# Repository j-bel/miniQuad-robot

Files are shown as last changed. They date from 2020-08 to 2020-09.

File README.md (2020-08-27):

# MiniQuad
### A Mini Quadrupedal Robot
CAD Files, Assembly Instruction, and Software Tutorials for a Miniature Quadrupedal Robot.  

MiniQuad

MiniQuad is a miniature quadruped robot capable of achieving four different leg joint configurations. It was created in order to test the impact of these different configurations on the quadruped's stability when it moves over a flat surface. The robot's body parts have been entirely 3D printed, allowing the robot to be extremely light weight. MiniQuad helps determine the viability of quadruped robots for different robotics research initiatives, as opposed to more traditional, wheeled robots, at a much lower cost.

### Design
The main design goals were to allow multiple leg-joint configurations while minimizing the weight of the robot. In order to do this, we relocated the motors from the joints themselves. The motors on the robot are offset from the joints through the use of timing belts. The motors that control the robot’s knees are actually located at its hip joints, and the motors that control its hip joints are located near the center of the robot’s sides. Apart from using 3D printed components, mounting the actuators on the main body, helped reduce the weight of the legs. Condensing its overall size also helped minimize the robot weight while maximizing the capabilities of the actuators by enabling them to reach higher angular velocities and increasing the overall speed of the robot.

Exploded Leg View

### Assembly

Building a MiniQuad requires access to a 3D printer, a phillips head screw driver, and a pair of pliers.

The Parts List and Links to order all off the shelf parts can be found in the [Master BOM](https://github.com/MiniQuad/robot/blob/master/Master%20BOM.md). 

All of the STL files for 3D printed parts can be found in [STL Files](https://github.com/MiniQuad/robot/tree/master/STL%20Files)

Detailed Assembly Instructions can be found in [Assembly Instructions](https://github.com/MiniQuad/robot/blob/master/Assembly%20Instructions.md)

### Experiments
Details about the experiments conducted can be found in [Experimentation](Experimentation.md)

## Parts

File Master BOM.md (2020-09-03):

<h1>Master BOM</h1>

| Part | Quantity per Robot |  Price | Link
| --- | :---: |--- | --- |
| <h3>Robotis Parts</h3> | | |
| Dynamixel XL-320  | 8 | $175.20 | http://www.robotis.us/dynamixel-xl-320/ |
| OpenCM9.04-C (with onboard XL-type connectors) | 1 | $19.90 | http://www.robotis.us/opencm9-04-c-with-onboard-xl-type-connectors/ |
| Li-ion Battery Charger Set LBB-041 | 2 | $15.80 | http://www.robotis.us/li-ion-battery-charger-set-lbb-041/ |
| Li-ion Battery 3.7V 1300mAh LB-041 | 2 | $19.80 | http://www.robotis.us/li-ion-battery-3-7v-1300mah-lb-041/ |
| <h3>McMaster-Carr Parts</h3> | | |
| 4.4in OD MXL Series Timing Belt  | 4 | $8.37 | https://www.mcmaster.com/7887K13/ |
| 5.6in OD MXL Series Timing Belt  | 4 | $11.60 | https://www.mcmaster.com/7887K15/ |
| Flat Head Screw 4-40 Thread Size, 1-1/4" Long  (50 Pack)| 1 | $4.40 |https://www.mcmaster.com/91771A117 |
| Washer, M2.5 Screw Size, 2.7 mm ID, 6 mm OD (100 pack) | 1 | $1.98 | https://www.mcmaster.com/93475A196/ |
| M2.5 x 0.45mm Thread, 16mm Long (100 pack) | 1 | $4.74 | https://www.mcmaster.com/92000A109/ |
| <h3>Amazon</h3> | | |
| eSUN PLA PRO (PLA+) 3D Printer Filament, Blue | 1 | $23.99 | [Amazon Filament](https://www.amazon.com/eSUN-1-75mm-Printer-Filament-2-2lbs/dp/B01EKEMNRO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) |
| HVAZI #4-40 UNC Machine Screws Nuts Assortment Kit | 1 | $12.99 | [Amazon 4-40 Screw Kit](https://www.amazon.com/HVAZI-Stainless-Phillips-Machine-Assortment/dp/B07GV31SDS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) |
| #4-40 Stainless Hex Lock Nut (100 Pack) | 1 | $6.98 | https://www.amazon.com/gp/product/B07HYNZXGV/ref=ppx_yo_dt_b_search_asin_title?ie=UTF8&psc=1 |
|<h4>Total Cost</h4>| | <h4>$305.75</h4> | |

<br/>
<br/>

<h3>Fasteners</h3>

| Part | Qty. |
| --- | :---: |
| 4-40 x 1.25" Countersunk | 4 |
| 4-40 x .75" Countersunk | 12 |
| 4-40 x .50" Coutnersunk | 16 |
| 4-40 x .375" Coutnersunk | 8 |
| 4-40 Locknut | 24 |
| 4-40 Hex Nut | 16 |
| M2.5 x 16mm | 8 |
| M2.5 Washer | 8 |
<br/>

<h3>3D Printed Parts</h3>

| Part | Filament per (g) | Qty | Filament Total (g)|
| --- | :---: |--- | --- |
| Base | 33.20 | 1 | 33.20 |
| Electronics Mount | 71.33 | 1 | 71.33 |
| Foot | 4 | | |
| Hip Pulley | 5.00 | 4 | 20.00 |
| Hip Pulley Brace | 5.78 | 4 | 23.12 |
| Knee Pulley | .54 | 4 | 2.16 |
| Leg | 1.96 | 4 | 7.84 |
| Leg Cover | 2.25 | 4 | 9.00 |
| Motor Hub | 3.75 | 4 | 15.00 |
| Motor Hub Connector | 3.35 | 4 | 13.40 |
| Thigh | 7.86 | 4 | 31.44 |
| Thigh Cover | 3.48 | 4 | 13.92 |
| XL320 Motor Mounts | 35.94 | 2 | 71.88 |
| Printing Total | | | 312.29 |

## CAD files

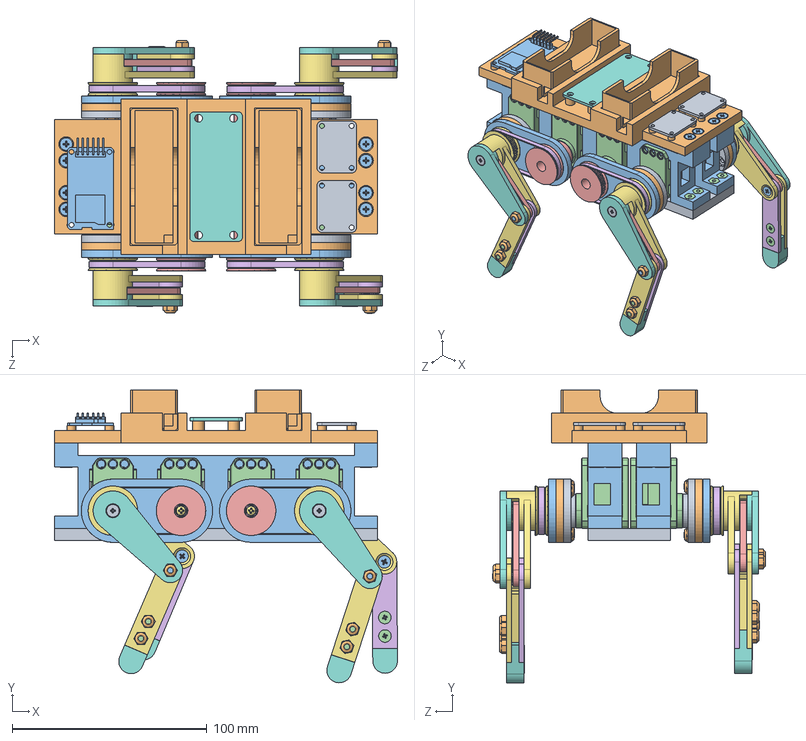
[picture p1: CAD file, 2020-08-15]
CAD/Mini Quad Assembly.SLDASM
176.2 x 150.3 x 140.2 mm
Base
Electronics Mount
XL320 Motor Mount x 2
XL-320 x 8
Hip Pulley x 4
5.6in Timing Belt x 4
Thigh x 4
Thigh Cover x 4
Motor Hub x 4
Motor Hub to Knee Pulley Connector x 4
Hip Pulley Brace x 4
Knee Pulley x 4
4.4in Timing Belt x 4
Leg x 4
Leg Cover x 4
Foot x 4
4-40 x 1.25 x 4
4-40 LockNut x 24
4-40x.75 x 12
4-40x.50 x 16
4-40x.375 x 8
M2.5 Washer x 8
M2.5 x 16mm x 8
Cm904Template
BNO055 9-DOF Orientation Sensor Template x 2
BatteryHolder x 2
sdreader
4-40 Nut x 16

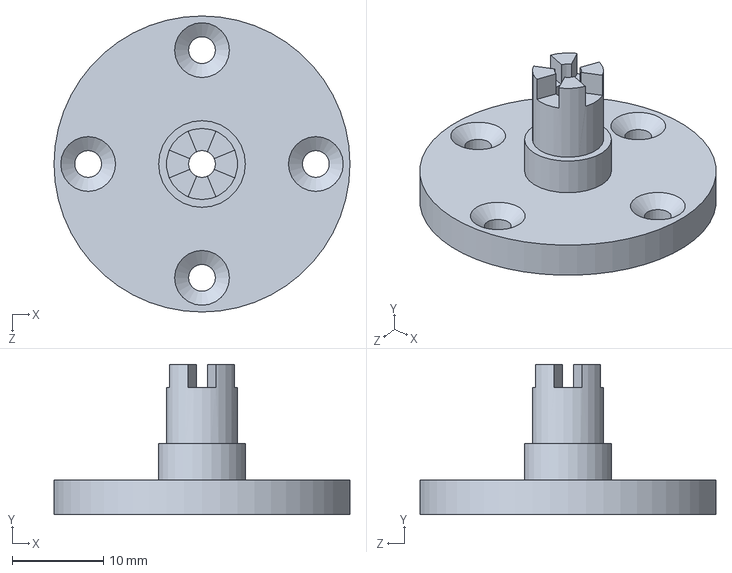
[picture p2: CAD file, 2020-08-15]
CAD/Motor Hub to Knee Pulley Connector.SLDPRT
32.5 x 16.5 x 32.5 mm

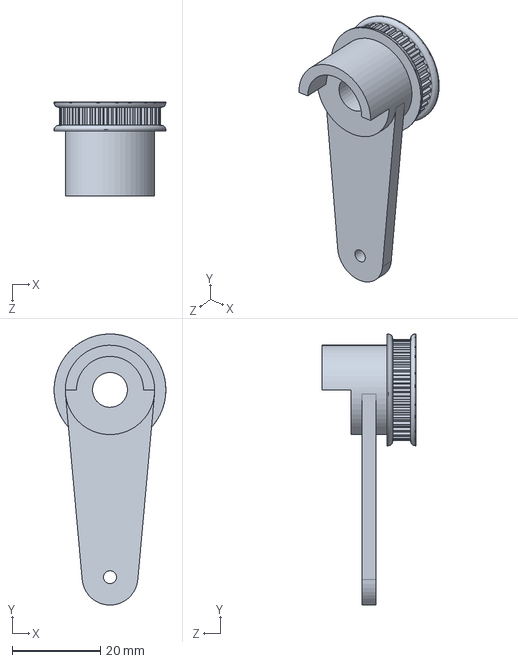
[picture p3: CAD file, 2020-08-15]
CAD/Thigh .SLDPRT
25.4 x 61.6 x 21.5 mm

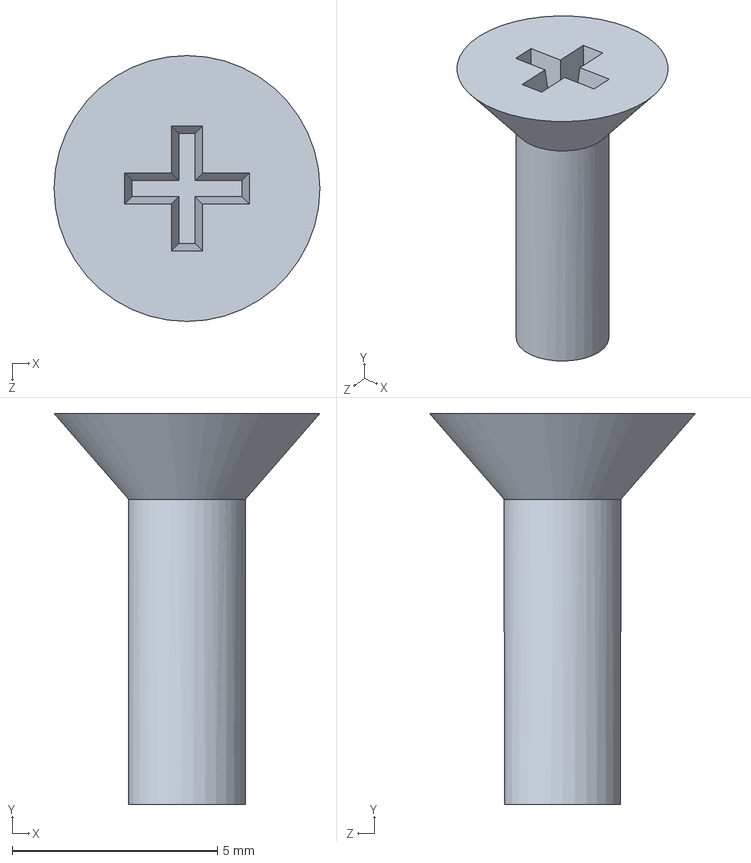
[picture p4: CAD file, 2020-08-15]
CAD/4-40x.375.SLDPRT
6.48 x 9.52 x 6.48 mm

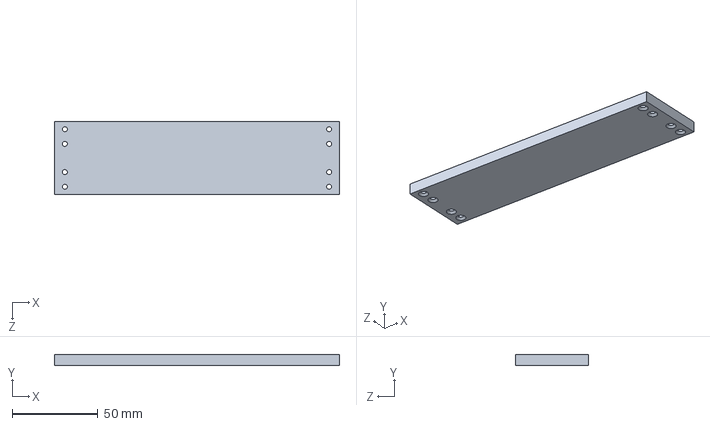
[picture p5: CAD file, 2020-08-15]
CAD/Base.SLDPRT
166.0 x 6.35 x 42.5 mm

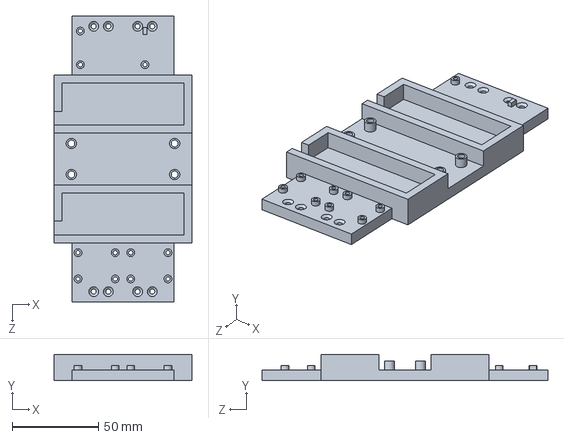
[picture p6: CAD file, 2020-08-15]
CAD/Electronics Mount.SLDPRT
80.0 x 15.4 x 166.0 mm

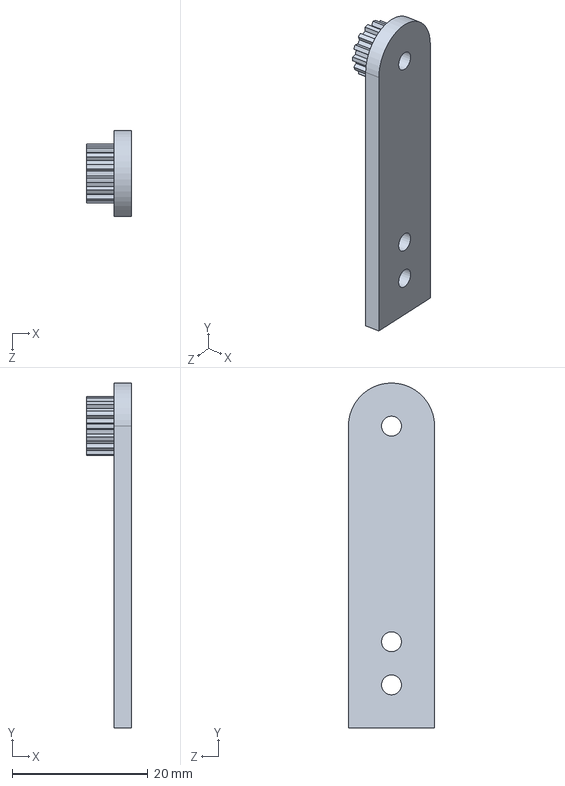
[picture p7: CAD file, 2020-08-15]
CAD/Leg.SLDPRT
6.60 x 50.8 x 12.7 mm

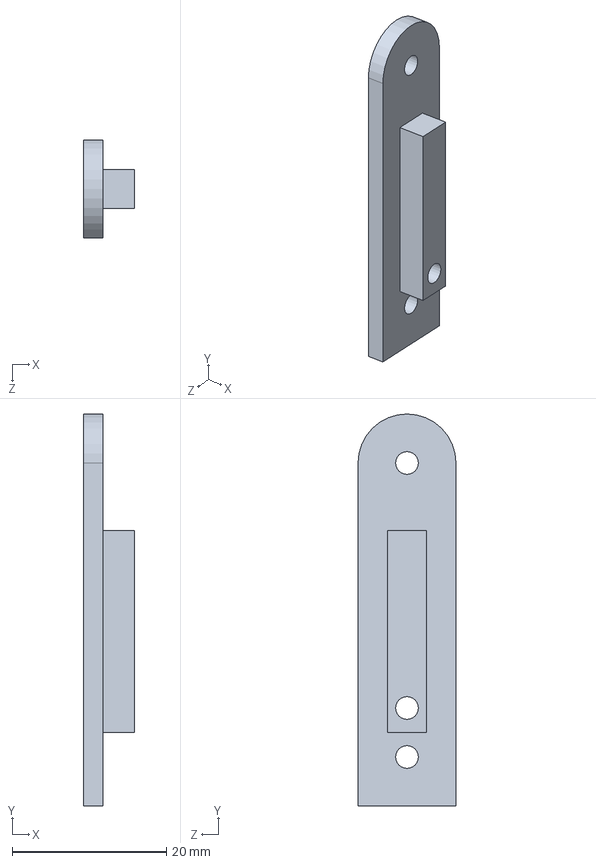
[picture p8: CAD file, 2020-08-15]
CAD/Leg Cover.SLDPRT
6.60 x 50.8 x 12.7 mm

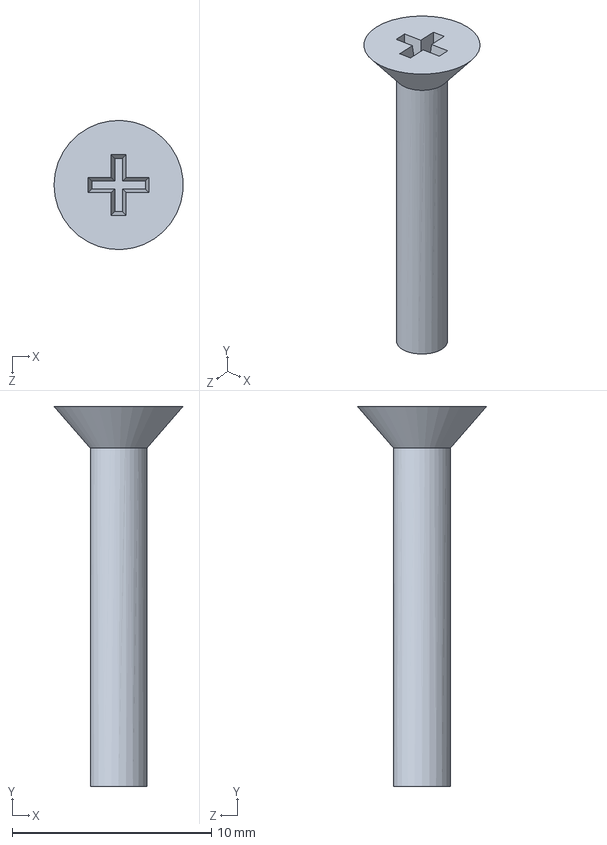
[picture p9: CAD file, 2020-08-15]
CAD/4-40x.75.SLDPRT
6.46 x 19.1 x 6.47 mm

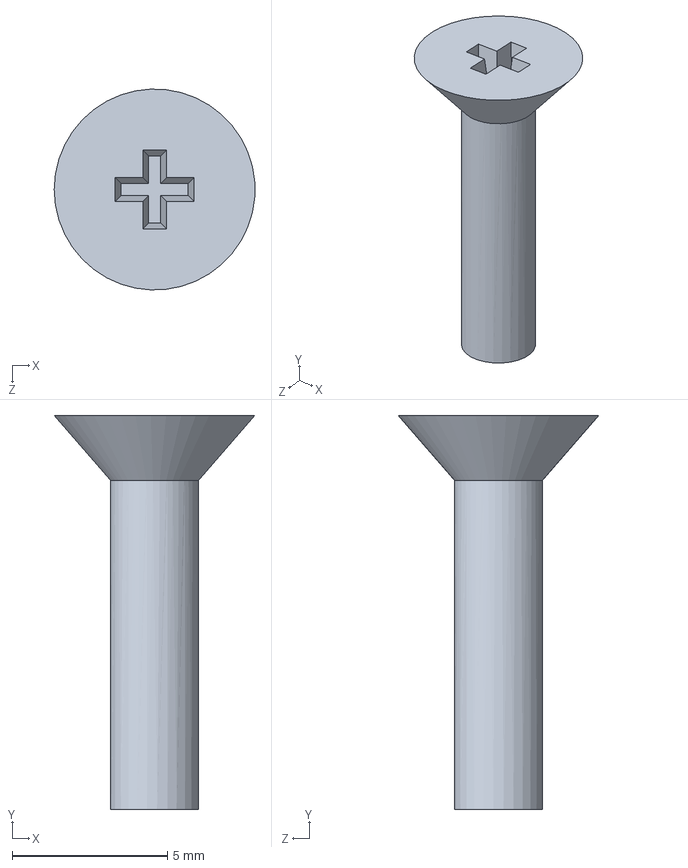
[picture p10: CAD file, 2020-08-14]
CAD/4-40x.50.SLDPRT
6.47 x 12.7 x 6.47 mm

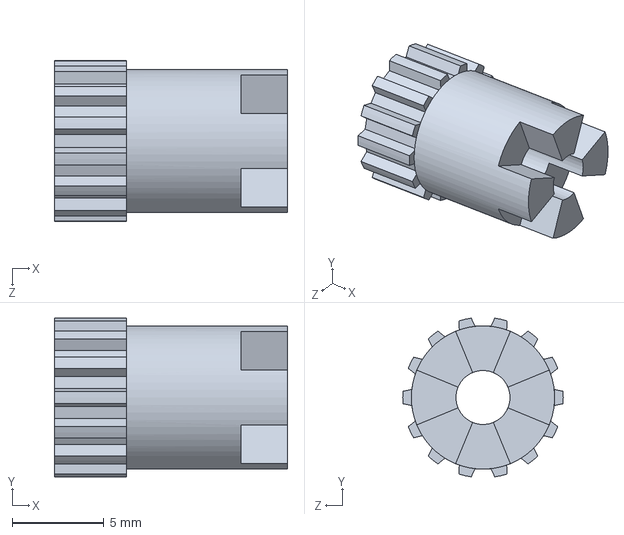
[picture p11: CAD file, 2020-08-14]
CAD/Knee Pulley.SLDPRT
12.7 x 8.66 x 8.75 mm

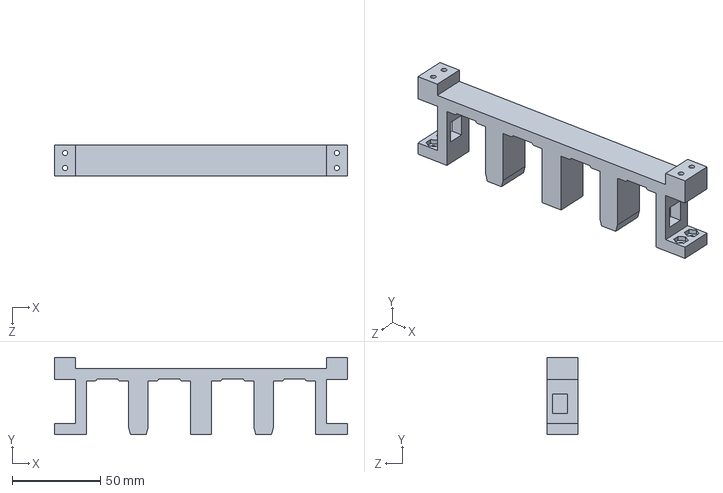
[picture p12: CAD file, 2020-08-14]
CAD/XL320 Motor Mount.SLDPRT
166.0 x 43.9 x 17.5 mm

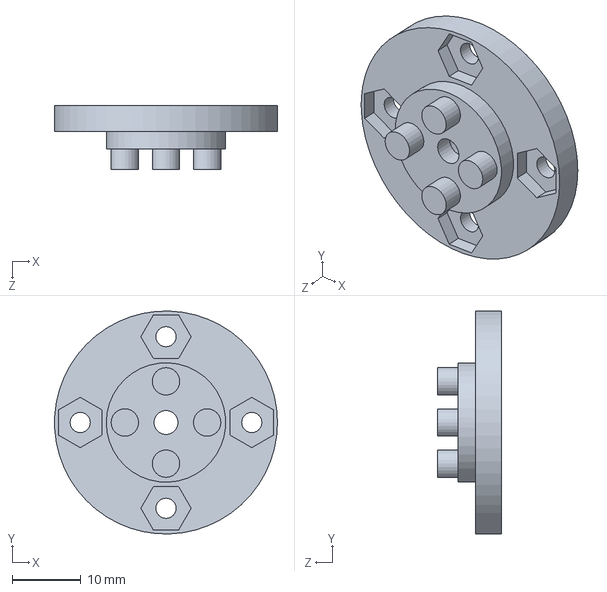
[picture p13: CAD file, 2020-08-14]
CAD/Motor Hub.SLDPRT
32.5 x 32.5 x 9.35 mm

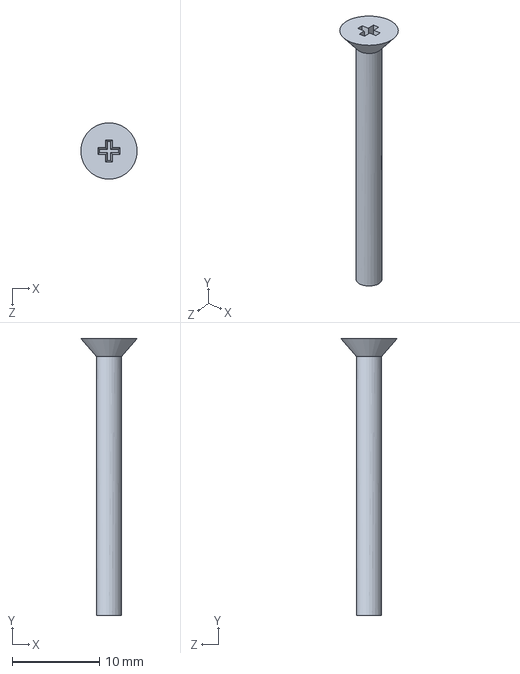
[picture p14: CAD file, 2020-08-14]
CAD/4-40 x 1.25.SLDPRT
6.48 x 31.8 x 6.48 mm

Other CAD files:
CAD/Foot.SLDPRT
CAD/5.6in Timing Belt.SLDPRT
CAD/Cm904Template.SLDPRT
CAD/BatteryHolder.SLDPRT
CAD/4-40 LockNut.SLDPRT
CAD/4-40 Nut.SLDPRT
CAD/4.4in Timing Belt.SLDPRT
CAD/BNO055 9-DOF Orientation Sensor Template.SLDPRT
CAD/Hip Pulley Brace.SLDPRT
CAD/Hip Pulley.SLDPRT
CAD/M2.5 Washer.SLDPRT
CAD/M2.5 x 16mm.SLDPRT
CAD/Thigh Cover.SLDPRT
CAD/XL-320.SLDPRT
CAD/sdreader.SLDPRT
STL Files/Base.STL
STL Files/Electronics Mount.STL
STL Files/Hip Pulley Brace.STL
STL Files/Hip Pulley.STL
STL Files/Knee Pulley.STL
STL Files/Leg Cover.STL
STL Files/Leg.STL
STL Files/Motor Hub to Knee Pulley Connector.STL
STL Files/Motor Hub.STL
STL Files/Thigh .STL
STL Files/Thigh Cover.STL
STL Files/XL320 Motor Mount.STL

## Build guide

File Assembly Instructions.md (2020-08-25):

# Assembly Instructions

#### Print and Acquire Parts

Begin by gathering all of the necessary material to build MiniQuad found in the [Master BOM](https://github.com/MiniQuad/robot/blob/master/Master%20BOM.md). Print the supplied [STL Files](https://github.com/MiniQuad/robot/tree/master/STL%20Files) in the quantities listed in the [Master BOM](https://github.com/MiniQuad/robot/blob/master/Master%20BOM.md). Note that all parts were sliced in the [PrusaSlicer](https://www.prusa3d.com/prusaslicer/) and printed on a [Prusa MK3S](https://shop.prusa3d.com/en/3d-printers/180-original-prusa-i3-mk3s-kit.html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) with a 40% infill. Depending on your slicer settings and 3D Printer, material used for each part can vary. You also may need to edit the parts depending on the tolerances of your 3D printer. SOLIDWORKS files are included in the [CAD](https://github.com/MiniQuad/robot/tree/master/CAD) folder in case edits are necessary.

#### Download OpenCM IDE

While the parts are printing, follow the steps to download the [OpenCM IDE](https://emanual.robotis.com/docs/en/software/opencm_ide/getting_started/) from robotis. The OpenCM IDE will be necessary to run the initial set up code as well as program MiniQuad to move. 

#### Assign Motor ID's
Follow the Steps in the [Assign Motor ID Instructions](https://github.com/MiniQuad/robot/blob/master/Assembly%20Files/1%20Assign%20Motor%20ID's.md) to assign each of the 8 motor's with an individual ID that will be later used to program MiniQuad.

#### Main Body Assembly
Follow the Steps in the [Main Body Assembly Instructions](https://github.com/MiniQuad/robot/blob/master/Assembly%20Files/2%20Main%20Body%20Assembly.md) to assemble the body of MiniQuad and attach all of the motors in the correct locations.

#### Leg Assembly
Follow the Steps in the [Leg Assembly Instructions](https://github.com/MiniQuad/robot/blob/master/Assembly%20Files/3%20Leg%20Assembly.md) to attach and assemble all of the legs on MiniQuad.

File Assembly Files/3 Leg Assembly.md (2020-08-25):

### Leg Assembly

Plug two batteries into the OpenCM9.04. Open the [SetZeroPosition](https://github.com/MiniQuad/robot/blob/master/Assembly%20Files/Assembly%20Code/SetZeroPosition.ino) code in the OpenCM IDE. Replace the numbers in the red box below to the numbers of the motors that you are currently assembling a leg on. The leg assembly shown in the instructions below correspond to motors 1 and 2. Upload the code to the OpenCM9.04. 

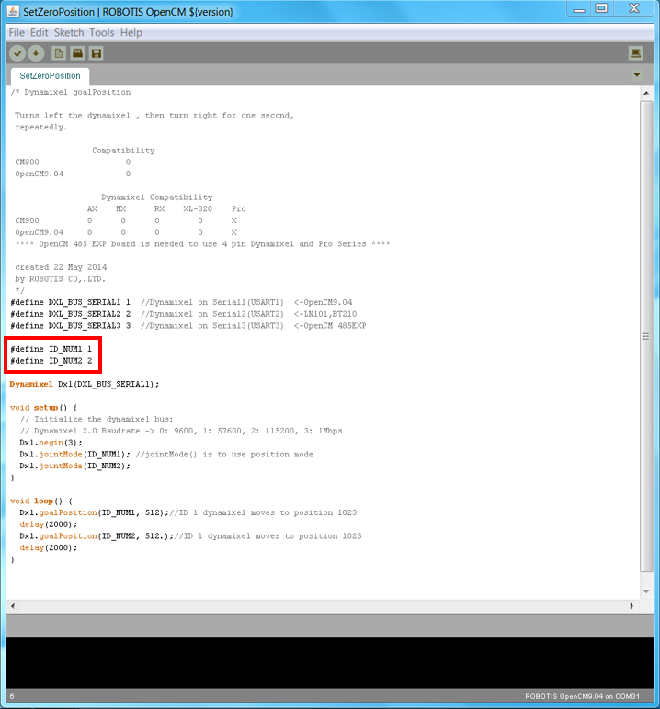
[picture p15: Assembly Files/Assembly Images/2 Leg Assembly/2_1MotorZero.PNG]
2_1MotorZero


Once the Code is uploaded, the motor should move to the position shown below where the notch on the base of the motor aligns with the notch on the horn of the motor. You can assemble the legs with the batteries and OpenCM9.04 unplugged, but it is recommended to leave them plugged in to prevent the motors from rotating at all during the assembly.

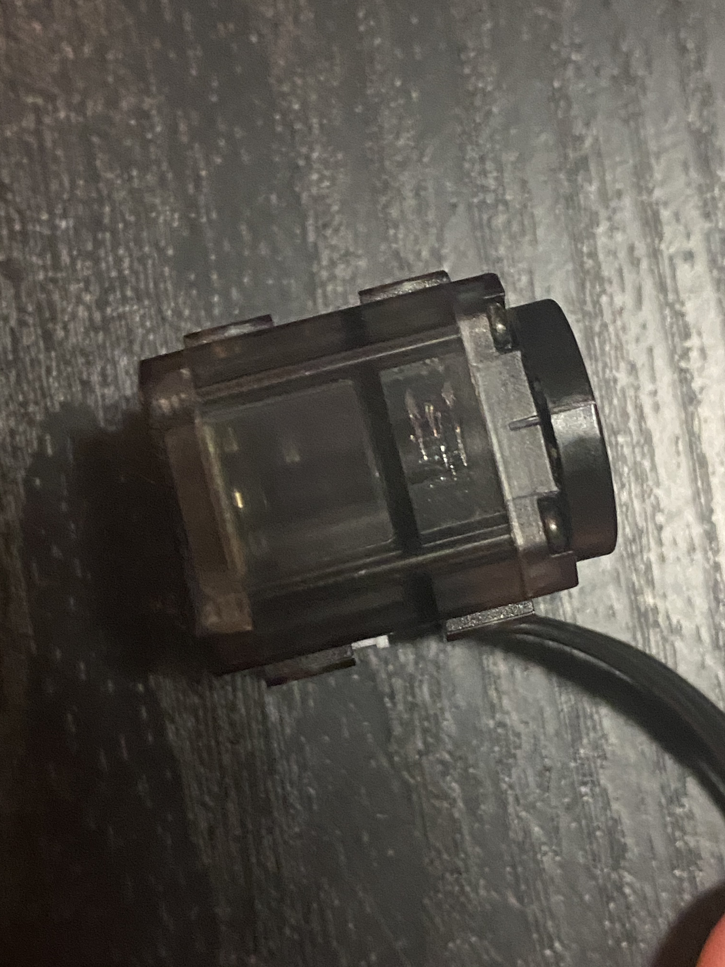
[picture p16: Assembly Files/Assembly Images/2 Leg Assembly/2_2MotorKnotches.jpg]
2_2MotorKnotches


Remove the screws from the XL-320 that hold the servo horn in place (circled below)

1RemoveScrew

Place 4-40 nuts (x2) into 2 of slots on the back of the Motor Hub. Any set of slots will work as long as they are both on the same diagonal of the rectangle formed by the 4 slots present.

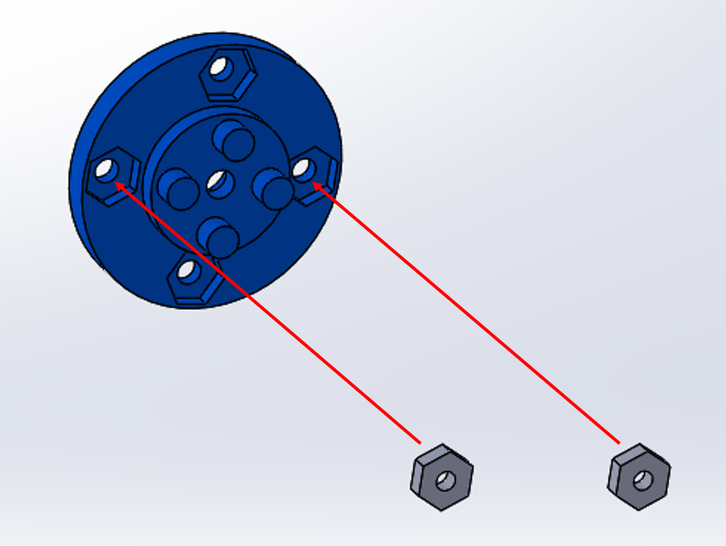
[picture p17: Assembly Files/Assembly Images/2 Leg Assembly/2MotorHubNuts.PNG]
2MotorHubNuts


Attach the Motor Hub to the horn of the XL-320. First press the Motor Hub into place. The registration tabs on the Motor Hub should align with the holes on the horn of the XL-320. Snap the tabs into place and fasten the hub onto the motor using an M2.5 x 16mm screw and an M2.5 Washer.

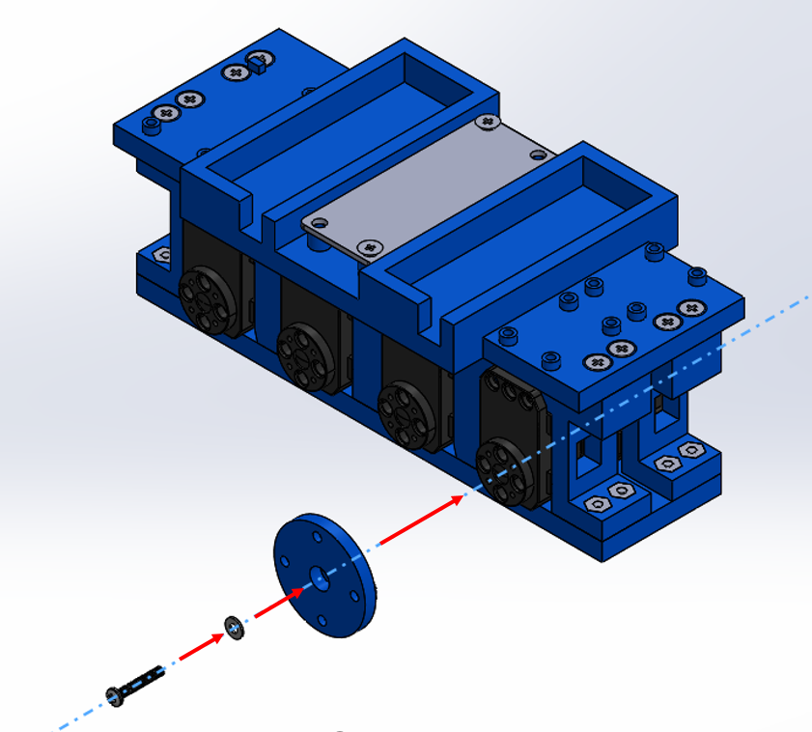
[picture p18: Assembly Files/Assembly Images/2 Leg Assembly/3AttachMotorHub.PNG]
3AttachMotorHub


Place a 4-40 Locknut into the slot on the back of the Motor Hub Connector. Make sure to push the Locknut as far into the connector as possible.

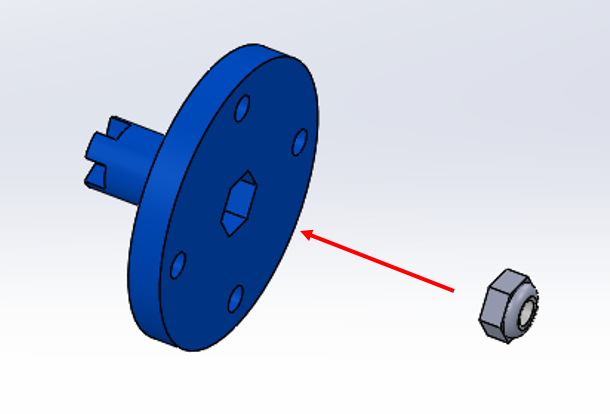
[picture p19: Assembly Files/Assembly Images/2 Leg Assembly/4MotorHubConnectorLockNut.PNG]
4MotorHubConnectorLockNut


Attach the Motor Hub Connector to the Motor Hub using 4-40 x .375" countersunk screws (x2). 

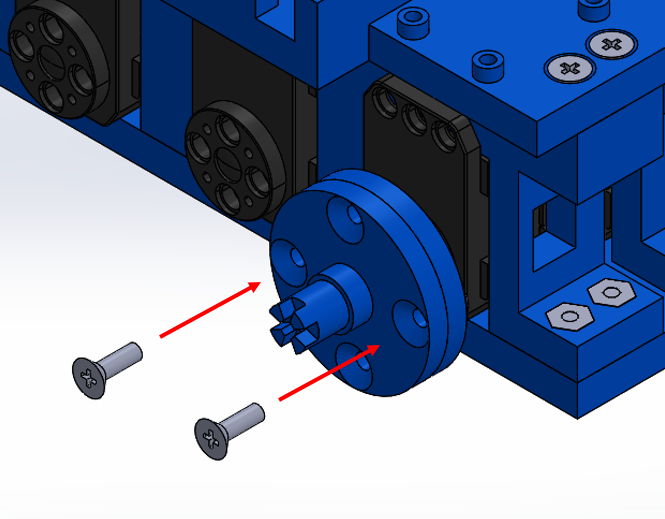
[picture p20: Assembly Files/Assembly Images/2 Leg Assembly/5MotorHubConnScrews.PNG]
5MotorHubConnScrews


Attach the Pulley Brace to the assembly by sliding the smaller hole of the brace onto the Motor Hub Connector.

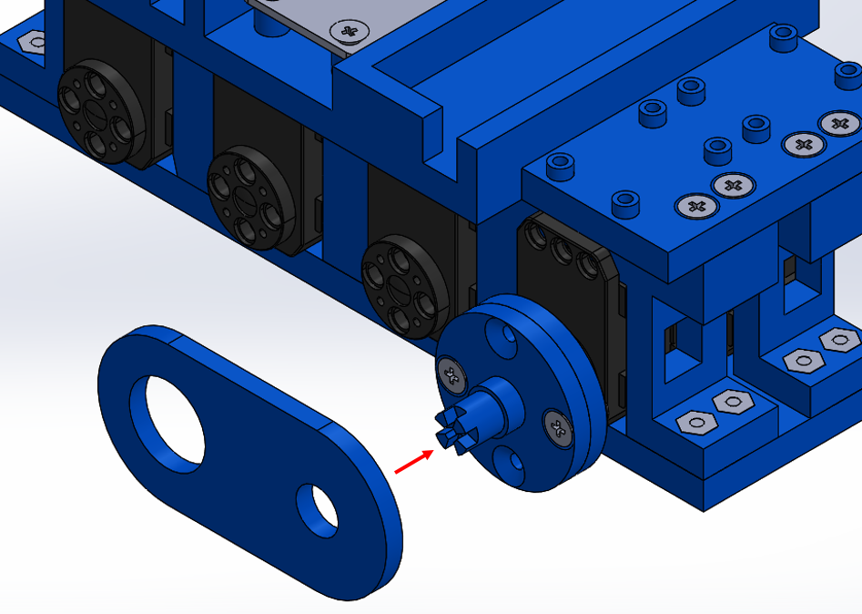
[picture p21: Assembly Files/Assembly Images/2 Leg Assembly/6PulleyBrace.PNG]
6PulleyBrace


Attach the Thigh Pulley to the assembly following the same steps as the Motor Hub. Align the registration tabs on the Thigh Pulley with the holes on motor 2 and snap it into place. Fasten the pulley to the motor using an M2.5 x 16mm screw and an M2.5 Washer.

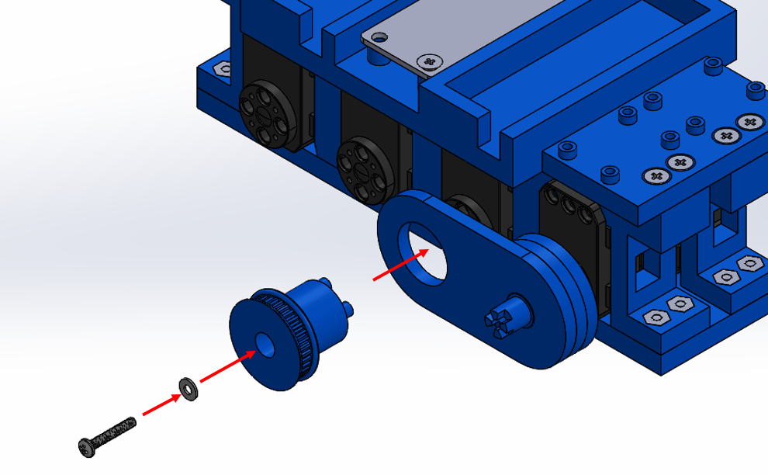
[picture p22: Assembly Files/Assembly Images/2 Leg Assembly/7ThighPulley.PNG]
7ThighPulley


Attach the 5.6" Timing Belt and Thigh to the Assembly. Wrap one end of the timing belt around the Thigh. Hold the thigh vertical to the assembly. Wrap the belt around the Thigh Pulley while sliding the thigh onto the Motor Hub Connector. Keep the thigh as vertical as possible during installation. Some deviation will be necessary to engage the timing belt. This will be corrected later during Motor Calibration.

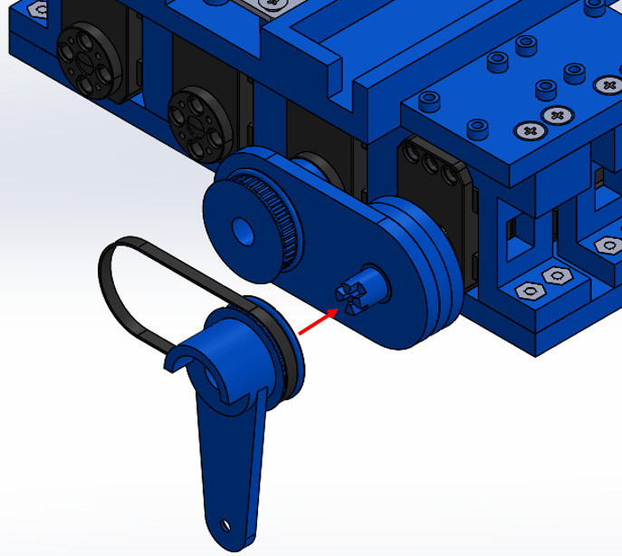
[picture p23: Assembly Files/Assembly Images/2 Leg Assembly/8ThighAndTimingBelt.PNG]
8ThighAndTimingBelt


Attach the Knee Pulley to the assembly by sliding it into the hole on the front of the Thigh. Align the registration tabs on the Knee Pulley to the slots on the Motor Hub Connector. Snap the Knee Pulley into place. The images on the right below depict the assembly with the Knee Pulley fully inserted into the leg assembly. The face of the teeth on the Knee Pulley should be sitting up agains the face of the thigh as seen in the bottom right image. 

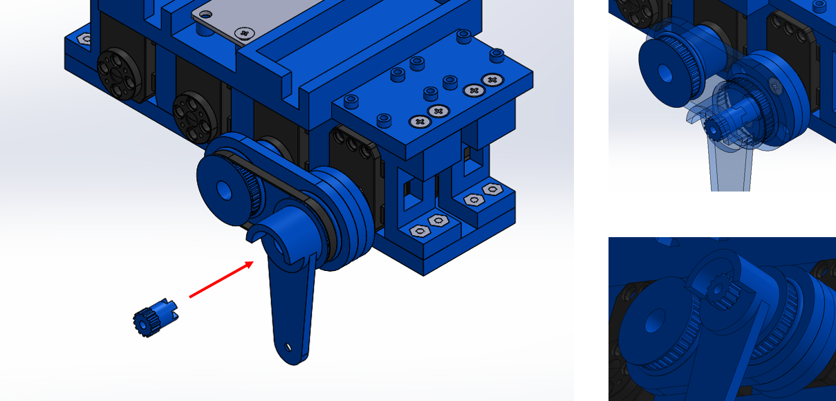
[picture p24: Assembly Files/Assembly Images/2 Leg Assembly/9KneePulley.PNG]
9KneePulley


Attach the Knee Cover to the Knee using a 4-40 x .5" countersunk screw and a 4-40 Locknut. Fasten the leg cover into place, but leave it loose enough for the Knee Cover to rotate around the axis of the screw.

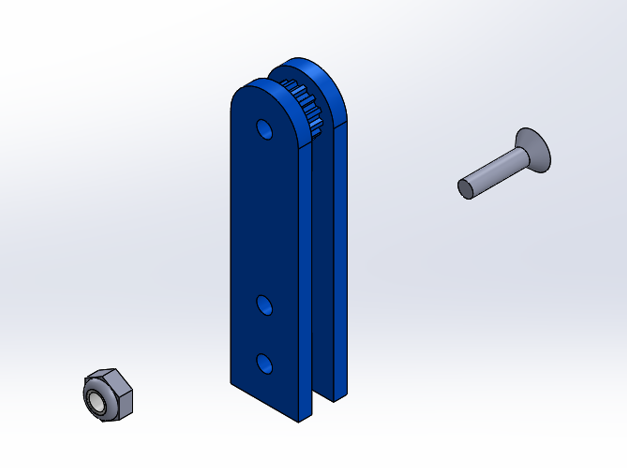
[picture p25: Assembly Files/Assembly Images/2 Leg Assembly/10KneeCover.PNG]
10KneeCover


Rotate the Knee Cover to one side enough to allow the 4.4" Timing Belt onto the teeth of the Knee.

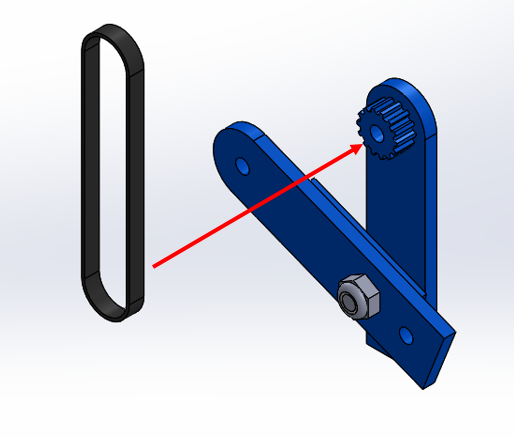
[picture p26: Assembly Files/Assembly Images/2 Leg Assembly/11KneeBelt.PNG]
11KneeBelt


Rotate the Knee Cover Back into place. Place the timing belt around the Knee Pulley at the top of the leg assembly. Stretch the Knee and Knee Cover downwards and put a 4-40 x .75" countersunk screw into the back of the Knee. If the fit is too tight, you may need to twist the screw into place. Make sure the back face of the knee is pressing up against the face of the Thigh.

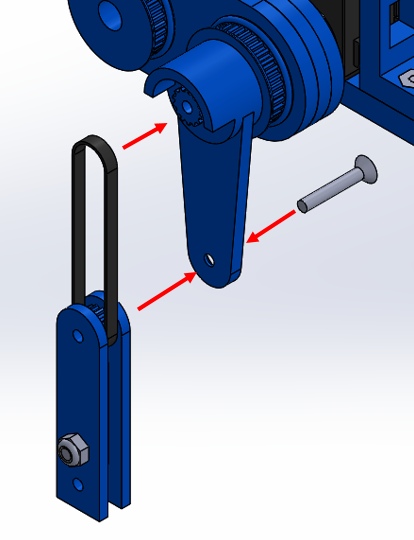
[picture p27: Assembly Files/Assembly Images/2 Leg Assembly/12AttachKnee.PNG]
12AttachKnee


Place the Thigh Cover onto the end of the 4-40 x .75" screw used in the previous step. Tighten it into place with a 4-40 Locknut. Make sure that the screw is not to tight and that the Thigh Cover can be rotated about the screw.

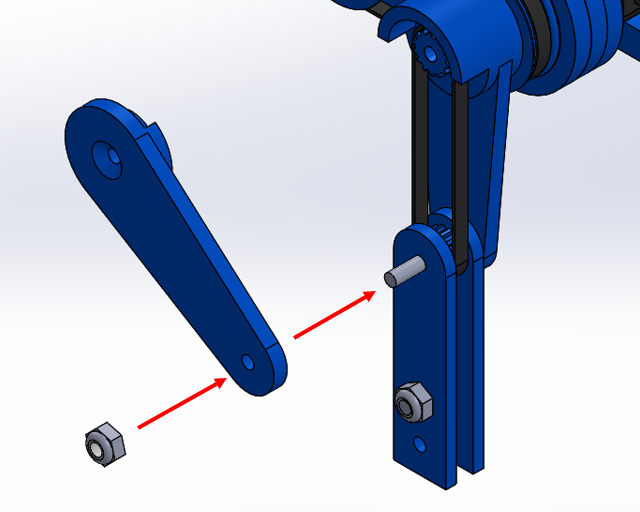
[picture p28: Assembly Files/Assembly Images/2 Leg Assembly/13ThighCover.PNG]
13ThighCover


Push on the bottom of the Knee in the direction and location of the yellow arrow in the image below. Rotated the top of the Thigh Cover into place. If the faces on the Thigh Cover don't sit flush against the faces of the Thigh, you made need to push more on the bottom of the foot. The assembly with flex a little bit, but do not push too hard as you may risk damaging the parts. Once the Thigh Cover is in place, fasten the assembly together using a 4-40 x 1.25" countersunk screw.

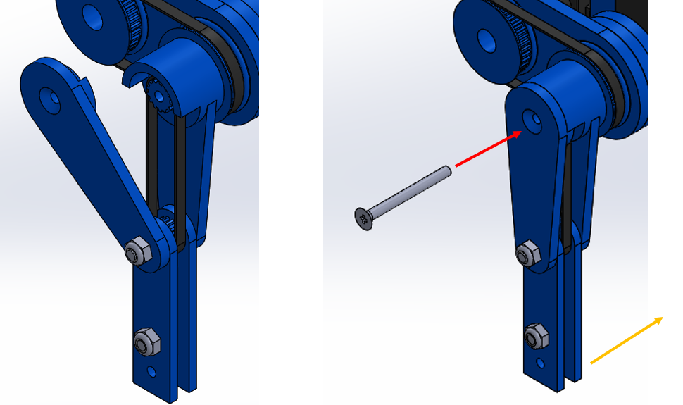
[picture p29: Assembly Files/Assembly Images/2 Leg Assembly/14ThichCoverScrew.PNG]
14ThichCoverScrew


Attach the foot to the assembly. Slide the Foot into place and tighten it to the bottom holes od the Knee and Knee Cover using a 4-40 x .50" countersunk screw and a 4-40 Locknut.

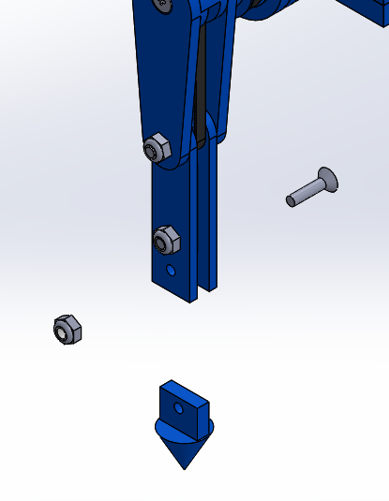
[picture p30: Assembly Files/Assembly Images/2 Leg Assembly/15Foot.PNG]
15Foot


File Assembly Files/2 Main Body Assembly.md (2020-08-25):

### Main Body Assembly

Lay the motors out in the orientation in the image below. 

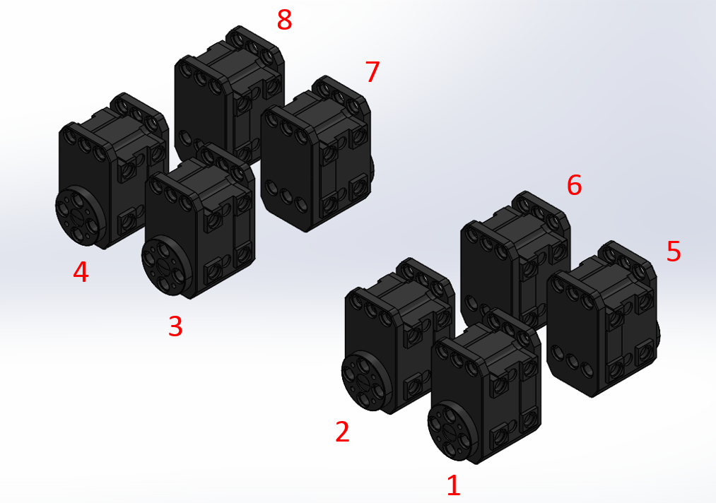
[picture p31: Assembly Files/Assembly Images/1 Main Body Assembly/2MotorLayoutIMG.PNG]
2MotorLayoutIMG


Connect Motor 1 to 2, 3 to 4, 5 to 6, and 7 to 8 with one of the supplied cables using inner terminals between each respective set of motors. Connect a second cable to the other terminals of motors 2, 3, 6, and 7. These terminals will be closest to the center of motor layout pictured above. Leave one end of the cable unnattached. This will be used to connect to the controller later.

Press a 4-40 Nut into each of the 4 holes on one of the XL320 Motor Mounts. 

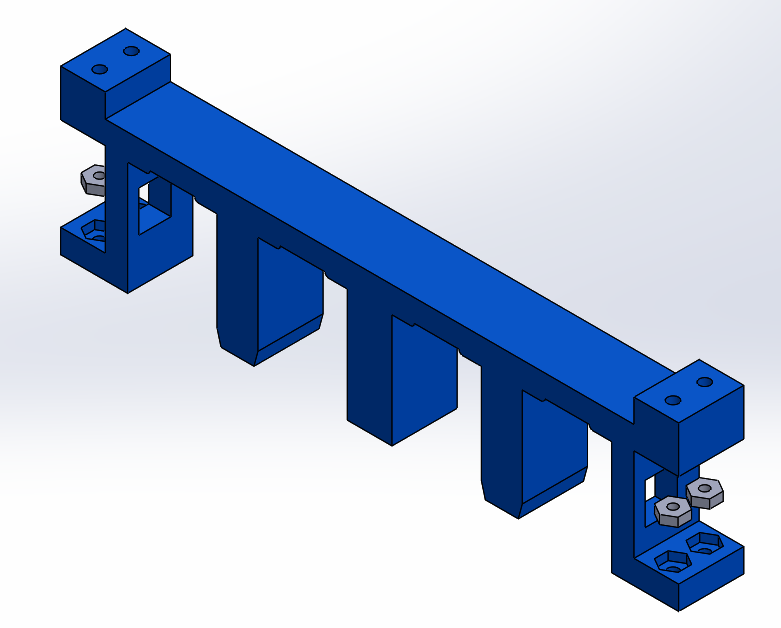
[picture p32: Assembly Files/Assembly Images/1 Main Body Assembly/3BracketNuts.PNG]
3BracketNuts


Slide Motors 1-4 into the bracket as shown below.

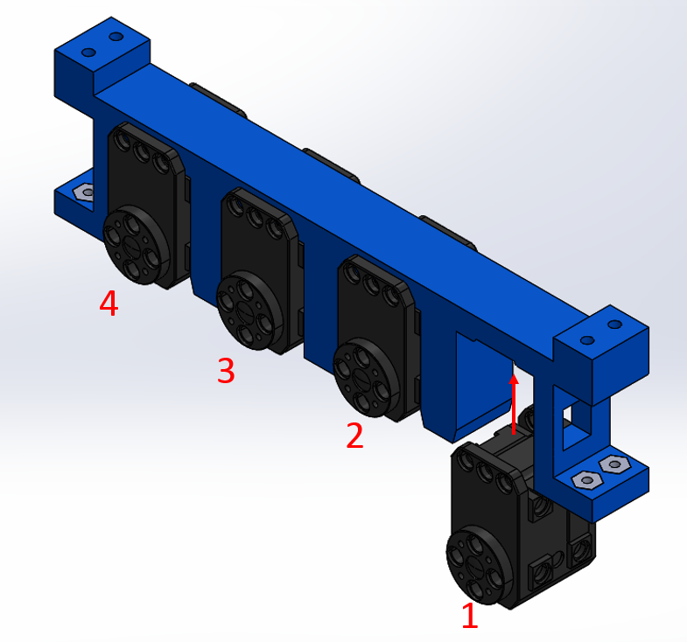
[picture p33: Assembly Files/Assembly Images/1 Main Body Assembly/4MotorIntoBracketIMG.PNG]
4MotorIntoBracketIMG


Repeat the previous 2 steps with motors 5-8. Note the Orientation and order of the motors when assembling.

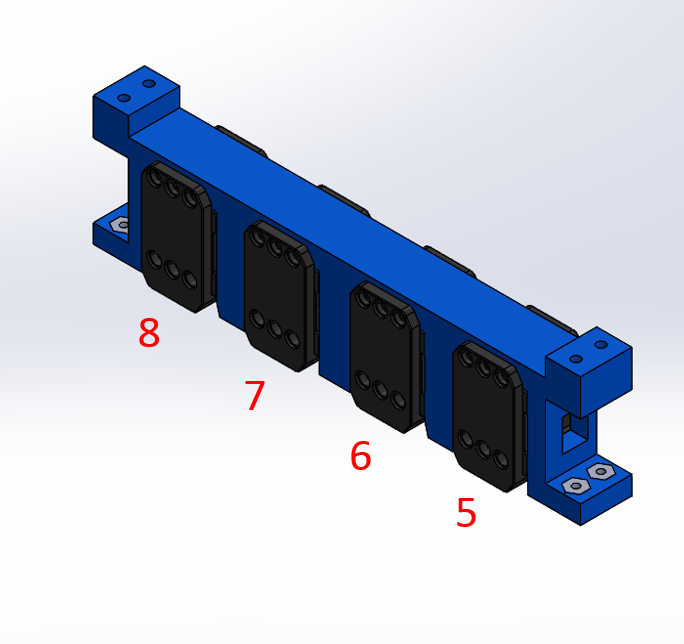
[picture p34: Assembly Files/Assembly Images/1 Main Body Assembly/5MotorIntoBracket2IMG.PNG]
5MotorIntoBracket2IMG


Attach both of the motor brackets to the base plate using 4-40 x .50" screws with countersunk heads (x8).

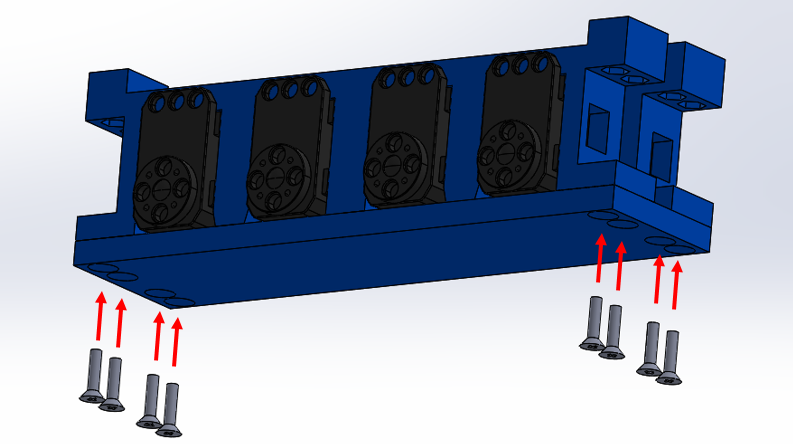
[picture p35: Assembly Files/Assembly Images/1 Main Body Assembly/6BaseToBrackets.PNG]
6BaseToBrackets


Attach the OpenCM9.04 board to the Electronics Mount using 4-40 x .50" screws. These can be countersunk, but flatheads are preferred. Note: other screw lengths over .50" may work as well.

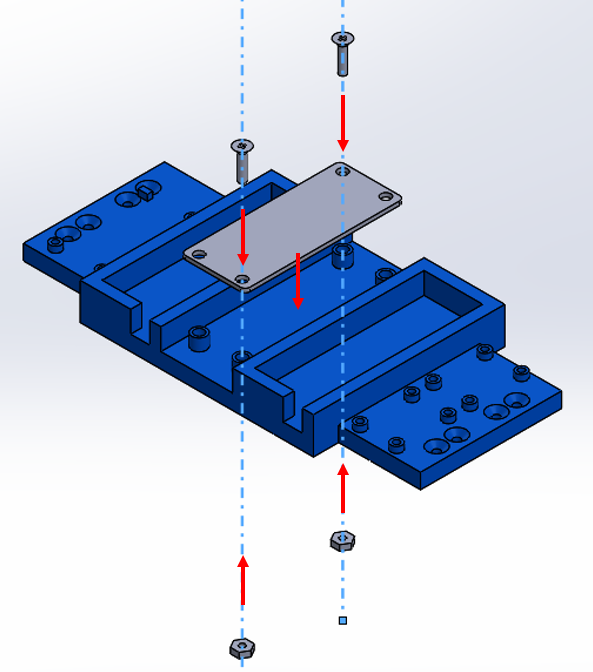
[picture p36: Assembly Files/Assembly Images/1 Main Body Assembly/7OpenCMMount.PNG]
7OpenCMMount


Attach the electronics mount to the assembly using 4-40 x .75" countersunk screws (x8) and 4-40 nuts (x8).

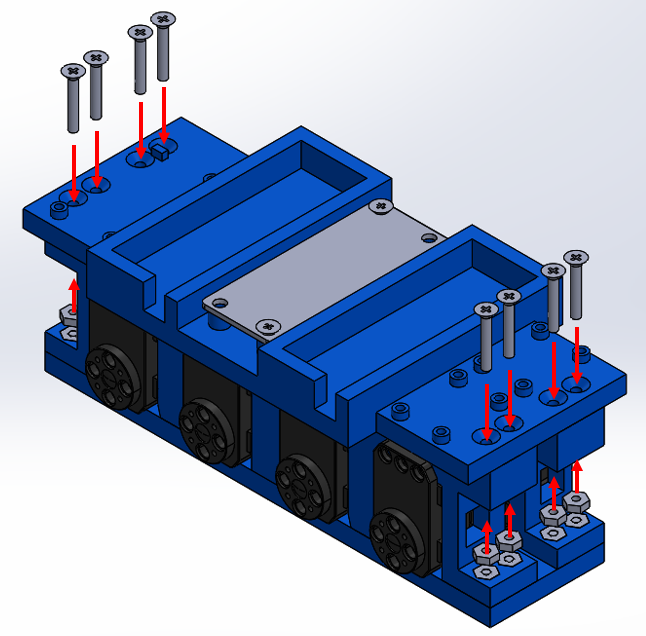
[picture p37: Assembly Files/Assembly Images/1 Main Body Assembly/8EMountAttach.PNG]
8EMountDOwn


After completing the above steps, the assembly should look as follows with the motor ID's corresponding to the numbers in the image below.

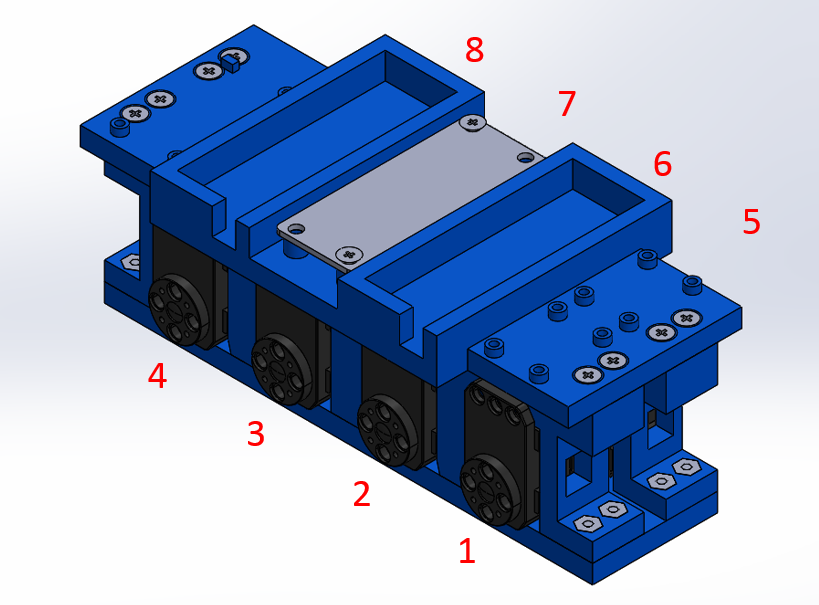
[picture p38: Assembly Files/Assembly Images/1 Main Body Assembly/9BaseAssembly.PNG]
9BaseAssembly


To finish the Main Body Assembly, plug the 4 remaining unconnected 3-wire cables into the 4 ports on the OpenCM 9.04 highlighted below
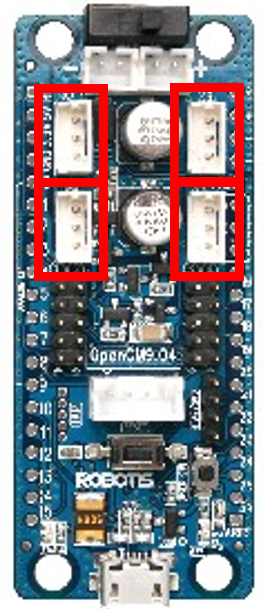
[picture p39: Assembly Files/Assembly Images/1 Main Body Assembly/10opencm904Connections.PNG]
10opencm904Connections


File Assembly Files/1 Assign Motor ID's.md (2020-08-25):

### Assign Motor ID's

Download and open [XL320_SetID](https://github.com/MiniQuad/robot/blob/master/Assembly%20Files/Assembly%20Code/XL320_SetID.ino) in the OpenCM IDE. 

Plug 2 charged batteries into the [OpenCM9.04](http://www.robotis.us/opencm9-04-c-with-onboard-xl-type-connectors/). 

Plug one of the [XL-320](http://www.robotis.us/dynamixel-xl-320/) Motors into the OpenCM9.04 using the 3 wire cable that comes with it. 

For this step, make sure only one motor is plugged in at a time!

Plug the OpenCM9.04 into a USB Port on your computer.  

Flip the switch on the OpenCM9.04 near the batteries to the on position. If you are unsure which way is the on position, you can unplug the OpenCM9.04 from your computer. The red light will remain on when unplugged if the switch is in the correct position. 

Edit the code so that the number in the red box pictured blow is the current ID you are assigning.

Upload the code. If the motor begins to rotate back and forth, its ID has been successfully set.

Label the Motor with its ID. This will be important for future assembling as well as programming the locomotion of MiniQuad

Repeat this step for all 8 XL-320 Motors, assigning each motor with an ID of 1-8 without repeating any numbers. 

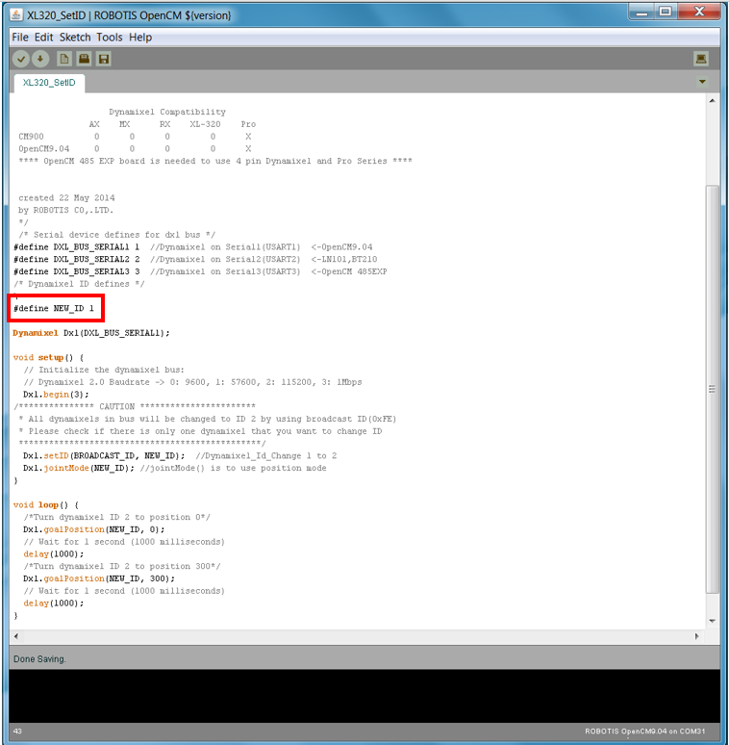
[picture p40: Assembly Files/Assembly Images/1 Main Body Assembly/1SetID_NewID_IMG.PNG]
1SetID_NewID_IMG


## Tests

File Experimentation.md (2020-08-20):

## Experiments

The four different leg joint configurations

MiniQuad's stability was evaluated for both the walking and running gait by observing inertial measurement unit (IMU) readings for roll and pitch and their derivatives as the robot traversed over a straight, 1 meter long flat course. This data was recorded for four different configurations as shown in the image above for both walking and running. Two different leg trajectories, one centered and one with an offset of 17.5 mm as shown below were also considered during experimentation.
Centered
Offset

For each experiment,five trials were conducted over eight different configuration-trajectory combinations.
The IMU readings for roll and pitch and their derivatives were stored in text files written to an SD card during the experiments. As this data was noisy and also contained readings before and after the duration of the experiment, data preprocessing was required before extracting useful information from it. The data from the text file was extracted and clipped to include the portion relevant to the experiment using MATLAB. It was desired to observe the rate at which the roll and pitch changed, and hence the derivatives were initially plotted to find that the curve was similar to an oscillation. The average amplitude of the oscillation was found for each trial and averaged over all trials on a specific joint configuration and gait to obtain the average rate at which it changed for that leg configuration and gait in order to assess the stability of the robot’s body.

### Observations
It was observed that the least rate of change in roll and pitch values for the walking gait was for configuration (b) and configuration (c) for the running gait suggesting that these could be the most stable leg configurations. However, these configurations were unable to produce gait when there leg trajectories were changed and hence it could not be concluded if these were the most stable. Configuration (d) was the only one to have produced gait for all trajectories and was also the most unstable.

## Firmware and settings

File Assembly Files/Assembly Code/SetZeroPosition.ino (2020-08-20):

/* Dynamixel goalPosition
 
 Turns left the dynamixel , then turn right for one second,
 repeatedly.
 
                 Compatibility
 CM900                  O
 OpenCM9.04             O
 
                   Dynamixel Compatibility
                AX    MX      RX    XL-320    Pro
 CM900          O      O      O        O      X
 OpenCM9.04     O      O      O        O      X
 **** OpenCM 485 EXP board is needed to use 4 pin Dynamixel and Pro Series ****
 
 created 22 May 2014
 by ROBOTIS CO,.LTD.
 */
#define DXL_BUS_SERIAL1 1  //Dynamixel on Serial1(USART1)  <-OpenCM9.04
#define DXL_BUS_SERIAL2 2  //Dynamixel on Serial2(USART2)  <-LN101,BT210
#define DXL_BUS_SERIAL3 3  //Dynamixel on Serial3(USART3)  <-OpenCM 485EXP

#define ID_NUM1 1
#define ID_NUM2 2

Dynamixel Dxl(DXL_BUS_SERIAL1);

void setup() {
  // Initialize the dynamixel bus:
  // Dynamixel 2.0 Baudrate -> 0: 9600, 1: 57600, 2: 115200, 3: 1Mbps  
  Dxl.begin(3);  
  Dxl.jointMode(ID_NUM1); //jointMode() is to use position mode
  Dxl.jointMode(ID_NUM2);
}

void loop() {
  Dxl.goalPosition(ID_NUM1, 512);//ID 1 dynamixel moves to position 1023
  delay(2000);
  Dxl.goalPosition(ID_NUM2, 512.);//ID 1 dynamixel moves to position 1023
  delay(2000);
}

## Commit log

2020-08-14 Create 3D Printed Parts List
2020-08-14 Update 3D Printed Parts List
2020-08-14 Rename Parts.md to 3D Printed Parts BOM.md
2020-08-14 Update 3D Printed Parts BOM.md
2020-08-14 Rename 3D Printed Parts BOM.md to 3D Printed Parts List.md
2020-08-15 Rename BOM.md to Master BOM.md
2020-08-17 Update Master BOM.md
2020-08-20 Create Assembly Instructions
2020-08-20 Rename Assembly Instructions to Assembly Instructions.md
2020-08-20 Update and rename Assembly Instructions.md to Experimentation.md
2020-08-20 Create Assembly Instructions.md
2020-08-20 Update Assembly Instructions.md
2020-08-25 Create Assign Motor ID's.md
2020-08-25 Rename Assign Motor ID's.md to 1 Assign Motor ID's.md
2020-08-25 Create 2 Main Body Assembly.md
2020-08-25 Create 3 Leg Assembly.md
2020-08-25 Update 3 Leg Assembly.md
